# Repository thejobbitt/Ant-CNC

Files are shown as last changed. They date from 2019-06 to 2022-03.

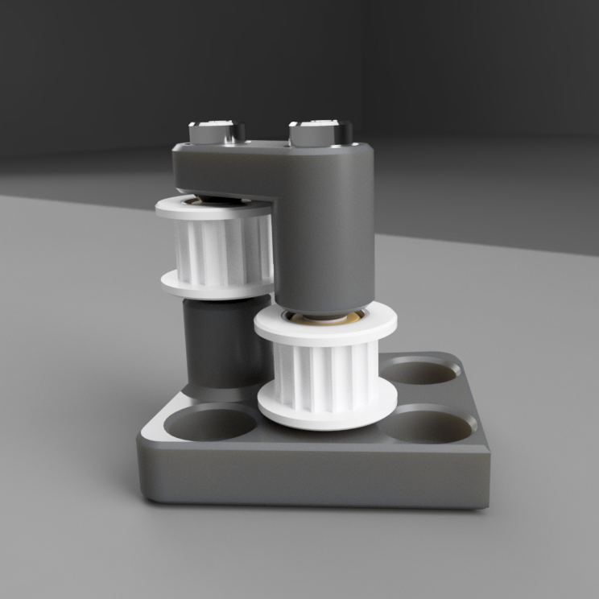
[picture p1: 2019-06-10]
images/wiki/GT2 Pulley Support Assembly v5.png

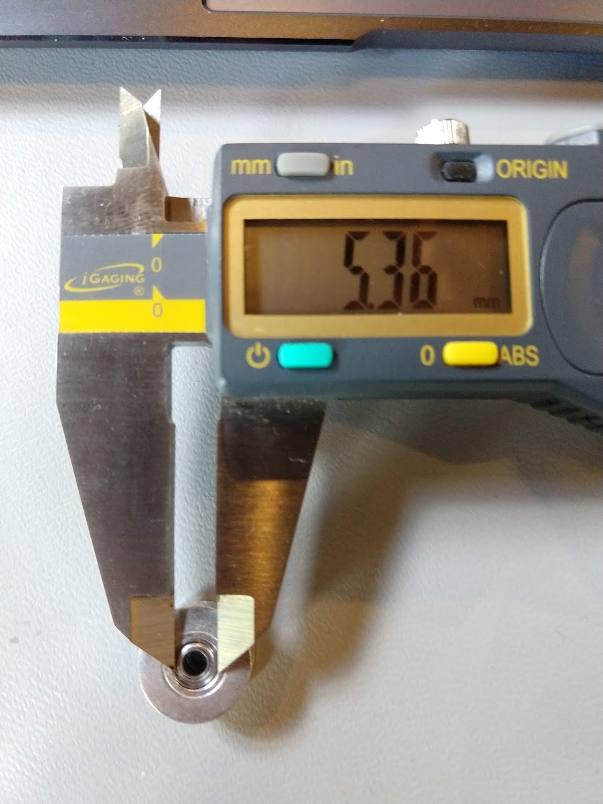
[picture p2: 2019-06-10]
images/wiki/outer_race_GT2_16T.jpg

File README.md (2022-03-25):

# Ant-CNC
Unofficial Ant CNC

This is a place to store the information I gather while building the Ant CNC. None of the upgrades are tested. Use at your own risk.

Any updates I make will be released with Fusion 360 files. If you wish to add to this repository send me a message.

Official github      -> https://github.com/TheAntTeam  
Official release     -> https://bitbucket.org/compactpcbmaker/cpcbm/src/master/  
Official youtube     -> https://www.youtube.com/channel/UCX44z-SSL7LzcB4xxgUdHHA/videos  
Official reddit      -> https://www.reddit.com/r/TheANT/  
Official facebook    -> https://www.facebook.com/groups/2238987226122714/  
Thingiverse Upgrades -> https://www.thingiverse.com/search?q=ant+pcb  

NOTE: All the files and informations in the mechanics folder of this repository are licensed under CC-BY-NC-SA license.

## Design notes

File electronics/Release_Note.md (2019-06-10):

14-04-2019 Modified Connection Scheme presentation.
Added also the link to the electronics assembly video as a reference, and added some more specific comments about:

-Nucleo F401RE board cap removal

-X and Y limit switches connections and checks.

-Spindle spinning direction.

12-02-2019 Added Connection Scheme presentation first draft.

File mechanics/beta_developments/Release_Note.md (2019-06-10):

# 23-04-2019
This is the Beta Developments folder where we share parts not yet released and under test.

Added head_4p2, an head modified to work with the Mistery D2632 blue and red version and brushless with up to 28 mm diameter.

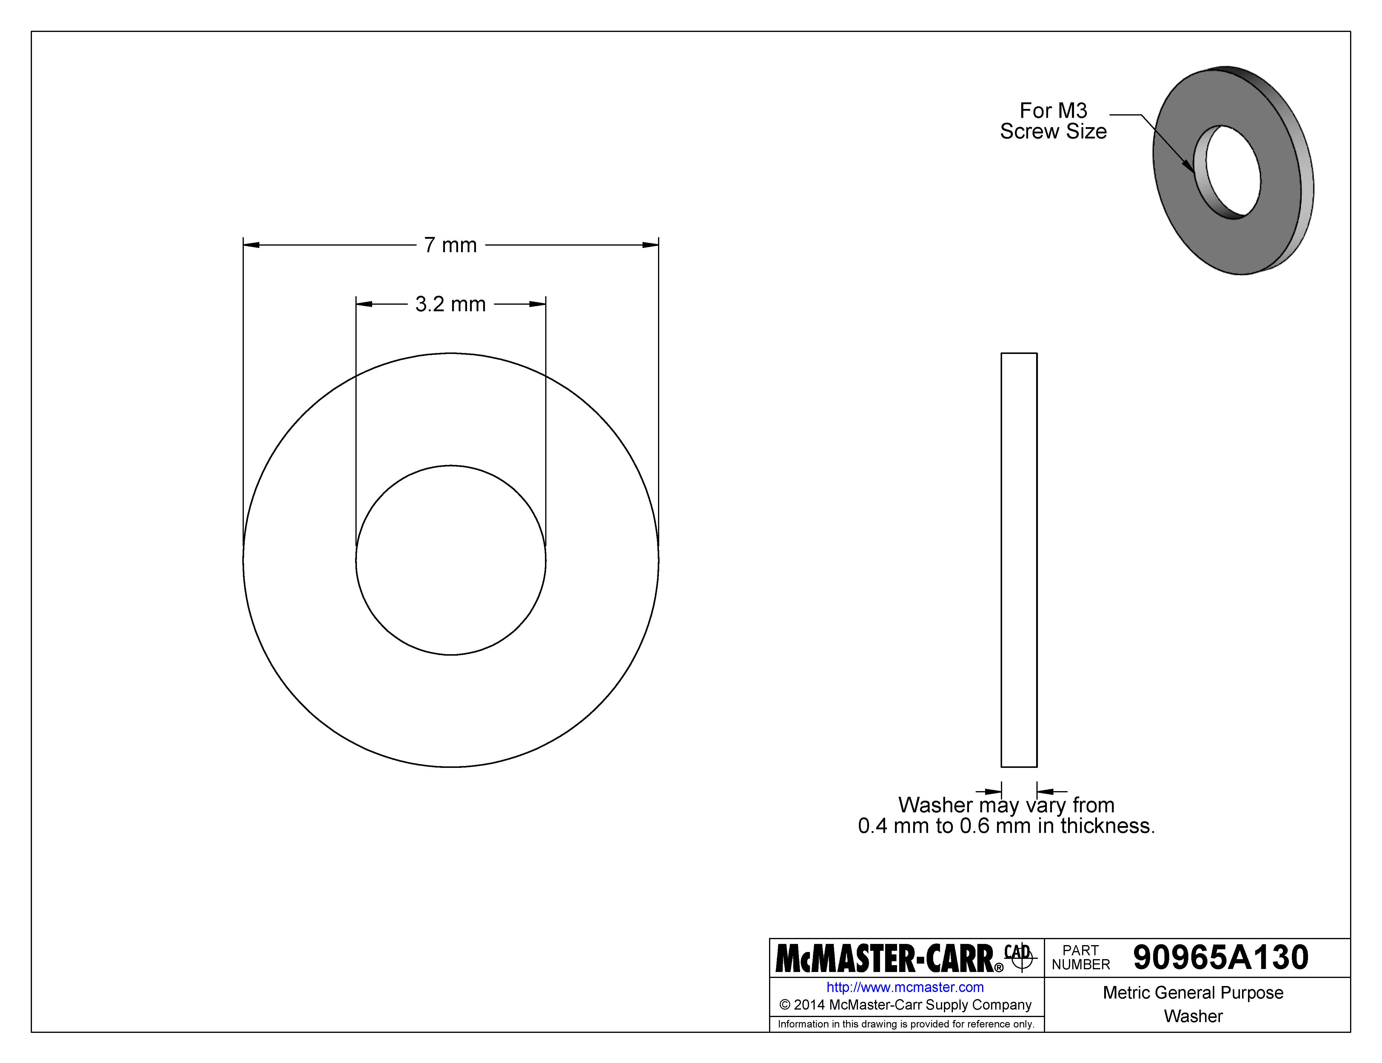
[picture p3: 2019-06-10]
images/wiki/3mm_flat_washer.jpg

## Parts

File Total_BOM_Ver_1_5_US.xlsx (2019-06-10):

Item | 1 | 2 | 3 | 4 | 5 | 6 | Qty | Brand | Ordered From | Part # | Cost | Qty if Pack | Unit Cost | Build Cost | Notes
Frame
10 x 10 x 200mm Aluminum Profile (black) | 8 |  |  |  |  |  | 8 | Makerbeam (kit) | Amazon | 100012 | $112.50 | 1 | 112.5 | $112.50
10 x 10 x 60mm Aluminum Profile (black) | 4 |  |  |  |  |  | 4 |  | ^
10 x 10mm Stainless Right Angle Bracket | 8 |  |  |  |  |  | 8 |  | ^
M3 x 0.5 x 6mm Square Headed Bolt | 47 |  |  |  |  |  | 47 |  | ^
Makerbeam T-slot nut | 24 |  |  |  |  |  | 24 | Makerbeam | Amazon | 101619 | $17.00 | 25 | 0.68 | $16.32
Hardware
M3 x 0.5 mm Lock Nut | 46 | 9 |  | 2 |  |  | 57 |  | McMaster | 90576A102 | $3.45 | 100 | 0.0345 | $1.97
M3 x 0.5mm Hex Nut | 4 |  |  |  |  | 8 | 12 |  | McMaster | 90591A250 | $2.21 | 100 | 0.0221 | $0.27
M5 x 0.8mm Hex Nut |  |  |  | 1 |  | 2 | 3 |  | McMaster | 90591A260 | $2.80 | 100 | 0.028 | $0.08
M2 x 0.4 x 8mm Socket Cap Bolt |  |  |  |  | 2 |  | 2 |  | McMaster | 91292A832 | $6.00 | 100 | 0.06 | $0.12
M2.5 x 0.45 x 8mm Socket Cap Bolt |  |  |  | 8 |  |  | 8 |  | McMaster | 91292A012 | $5.15 | 100 | 0.0515 | $0.41
M4 x 0.5 x 4mm Button Head Bolts (ISO 7380) | 8 |  |  |  | 4 |  | 12 |  | McMaster | 91239A109 | $8.50 | 25 | 0.34 | $4.08
M3 x 0.5 x 6mm Socket Cap Bolt | 12 | 9 |  | 2 | 3 |  | 26 |  | McMaster | 91292A111 | $9.18 | 100 | 0.0918 | $2.39
M3 x 0.5 x 8mm Socket Cap Bolt |  |  |  |  | 4 |  | 4 |  | McMaster | 91292A112 | $4.29 | 100 | 0.0429 | $0.17
M3 x 0.5 x 10mm Socket Cap Bolt |  | 4 |  |  |  | 8 | 12 |  | McMaster | 91292A113 | $4.72 | 100 | 0.0472 | $0.57
M3 x 0.5 x 16mm Socket Cap Bolt | 2 |  |  |  | 4 |  | 6 |  | McMaster | 91292A115 | $5.58 | 100 | 0.0558 | $0.33
M3 x 0.5 x 20mm Socket Cap Bolt | 8 |  |  | 1 |  |  | 9 |  | McMaster | 91292A123 | $6.44 | 100 | 0.0644 | $0.58
M3 x 0.5 x 25mm Socket Cap Bolt |  |  |  | 2 |  |  | 2 |  | McMaster | 91292A020 | $6.87 | 100 | 0.0687 | $0.14
M3 x 0.5 x 30mm Socket Cap Bolt | 4 |  |  |  |  |  | 4 |  | McMaster | 91292A022 | $4.08 | 50 | 0.0816 | $0.33
M3 x 0.5 x 50mm Socket Cap Bolt |  | 2 |  |  | 4 |  | 6 |  | McMaster | 91292A026 | $3.76 | 25 | 0.1504 | $0.90
M5 x 0.8 x 16mm Hex Head Bolt |  |  |  |  |  | 2 | 2 |  | McMaster | 91287A124 | $6.73 | 50 | 0.1346 | $0.27
M3 Lock Washer (ID 3mm, OD 5.5mm) | 8 | 14 |  |  |  |  | 22 |  | McMaster | 93925A220 | $3.45 | 100 | 0.0345 | $0.76
M3 Washer (ID 3mm, OD 7.5mm) | 16 | 10 |  |  |  |  | 26 |  | McMaster | 91166A210 | $1.69 | 100 | 0.0169 | $0.44
M3 x 0.5 x 100mm Threaded Rod |  | 3 |  |  |  |  | 3 | EasyScope | AliExpress |  | $2.89 | 5 | 0.578 | $1.73
3 x 16mm (#4 - 5/8") Flat Wood Screw |  |  |  |  |  | 6 | 6 | Midwest Fastner | Menards | 2524 | $2.13 | 100 | 0.0213 | $0.13 | Local
Bearings and Rails
GT2 Pulley 16T, 3mm Bore, 6mm Belt (w/ Bearings) | 4 | 2 |  |  |  |  | 6 | Powge | AliExpress |  | $12.60 | 7 | 1.8 | $10.80
GT2 Pulley, No Teeth, ID 3mm, 6mm Belt (w/ Bearings) |  | 2 |  |  |  |  | 2 | Powge | AliExpress |  | $5.40 | 3 | 1.8 | $3.60
GT2 Pulley 16T, ID 5mm, 6mm Belt, Set Screw (w/ Bearings) |  |  |  | 2 |  |  | 2 | Powge | AliExpress |  | $4.99 | 5 | 0.998 | $2.00
GT2 Timing Belt, 6mm Width, 1 Meter Length |  |  |  | 2 |  |  | 2 | Powge | AliExpress |  | $1.99 | 1 | 1.99 | $3.98
GT2 Timing Belt Locking Torsion Spring | 2 |  |  |  |  |  | 2 | Ali Life Store | AliExpress | SKU135539-3 FFIO PCK | $1.65 | 20 | 0.0825 | $0.16 | Check type
MGN9H Linear Rail 9mm x 200 mm | 2 |  |  |  |  |  | 2 | CNA Mecchanical Parts | AliExpress |  | $10.80 | 1 | 10.8 | $21.60
LM6UU Bearing |  | 8 |  |  |  |  | 8 | uxcell | Amazon | 709874355093 | $12.01 | 10 | 1.201 | $9.61
706C Bearing |  | 2 |  |  |  |  | 2 | Mochu | AliExpress |  | $5.00 | 1 | 5 | $10.00
6 x 180mm Chrome Plated Rod (200mm is Okay) |  | 2 |  |  |  |  | 2 | CNC Factory | AliExpress |  | $3.66 | 2 | 1.83 | $3.66
6 x 100mm Chrome Plated Rod |  | 2 |  |  |  |  | 2 | CNC Factory | AliExpress |  | $2.61 | 2 | 1.305 | $2.61
Spindle
ER8M C6 60L Extension Rod Chuck (w/ 1/8" Spring Collet) |  |  |  | 1 |  |  | 1 | HOZLY | AliExpress |  | $12.59 | 1 | 12.59 | $12.59
Lock Collar (Ring) w/ Set Screw, ID 6 mm, OD 12mm, 8mm Width |  |  |  | 1 |  |  | 1 | Victory 3D | AliExpress |  | $0.39 | 1 | 0.39 | $0.39
O-Ring ID 17mm, 2mm Thick |  |  |  |  |  | 2 | 2 | Hands Online | AliExpress |  | $0.36 | 10 | 0.036 | $0.07
Motors
NEMA - 11 - JK28HS51-674 |  |  | 2 |  |  |  | 2 | StepperOnline | Amazon | 11HS18-0674S | $18.90 | 1 | 18.9 | $37.80
Z Axis Stepper Linear Actuator - LC1574W-04-025 |  |  |  | 1 |  |  | 1 | Haydon | eBay | LC1574W-04-025 | $14.50 | 1 | 14.5 | $14.50
M12 Nut w/ Step 1.75mm, 5mm Thick (Included with Actuator) |  |  |  | 1 |  |  | 1 |  | ^
1000KV 2632 Brushless Outrunner Motor |  |  | 1 |  |  |  | 1 | Mistery | AliExpress | 2632-1000 | $25.39 | 1 | 25.39 | $25.39
Electronics
ESC 20A (for Brushless) |  |  | 1 |  |  |  | 1 | Gallop RC | AliExpress |  | $9.12 | 1 | 9.12 | $9.12
Nucleo F401RE |  |  |  |  | 1 |  | 1 | ST | Digikey |  | $13.83 | 1 | 13.83 | $13.83
CNC Arduino Shield V3 |  |  |  |  | 1 |  | 1 | Witbot (kit) | Amazon |  | $11.99 | 1 | 11.99 | $11.99
Stepstick Stepper Driver (A4988) |  |  |  |  | 3 |  | 3 |  | ^
2.54mm Jumper |  |  |  |  | 10 |  | 10 |  | ^
Mechanical Limit Switch Module Vertical |  | 2 |  |  |  |  | 2 | H X Y | AliExpress |  | $1.58 | 1 | 1.58 | $3.16
Mechanical Endstop Micro Switch w/ Dupont Terminal |  |  | 1 |  |  |  | 1 | AirMail | AliExpress |  | $1.51 | 1 | 1.51 | $1.51
Round Rocker Switch, SPST, 12v, 14mm panel hole |  |  |  |  | 1 |  | 1 | USMEI | Amazon |  | $6.49 | 2 | 3.245 | $3.25
12V brushless 40x40x10mm fan |  |  |  |  | 1 |  | 1 | Noctua | Amazon | NF-A4x10 | $13.95 | 1 | 13.95 | $13.95
12V 10A Power Supply, 5.5mm x 2.5mm DC Plug |  |  |  |  |  | 1 | 1 | COOLM | Amazon | HJDZ-1210 | $21.99 | 1 | 21.99 | $21.99
Wire and Connectors
3.5mm Bullet Connector Male |  |  | 3 |  |  |  | 3 | Apex RC | Amazon | 1102 | $7.99 | 10 | 0.799 | $2.40
3.5mm Bullet Connectors Female |  |  | 2 |  |  |  | 2 | Apex RC | ^
JST 1x04 Connector Male |  |  | 1 |  |  |  | 1 | Hilitch | Amazon |  | $10.69 | 200 | 0.05345 | $0.05
Dupont 1x04 Connector Female Housing |  |  | 2 |  |  |  | 2 | FUNMANY (kit) | Amazon |  | $13.99 | 200 | 0.06995 | $0.14
Dupont 1x03 Connector Female Housing |  |  | 2 |  |  |  | 2 |  | ^
Dupont Female Pin |  |  | 14 |  |  |  | 14 |  | ^
Alligator Clip w/ Cover |  |  | 2 |  |  |  | 2 |  | McMaster | 7236K55 | $0.94 | 1 | 0.94 | $1.88
Extension Servo Lead Wire Male to Female 10 cm cable |  |  | 1 |  |  |  | 1
Cable 26 AWG about 40 cm |  |  | 4 |  |  |  | 4
Cable 16 AWG about 40 cm |  |  | 2 |  |  |  | 2
Cable 16 AWG about 20 cm |  |  |  |  | 2 |  | 2
Dupont cable Female to Female 20 cm |  |  |  |  | 2 |  | 2
5.5mm x 2.1mm DC Power Jack, Barrel, Panel Mount |  |  |  |  | 1 |  | 1 | Switchcraft | Digikey | SC3508-ND | $3.99 | 1 | 3.99 | $3.99
3.5mm Stereo earphone with jack 3.5mm |  |  | 1 |  |  |  | 1 | CUI Inc | Digikey | MP3-3501 | $1.04 | 1 | 1.04 | $1.04
3.5mm Stereo Headphone Jack, Panel Mount |  |  |  |  | 1 |  | 1 | Nine to Nine | Amazon |  | $6.99 | 10 | 0.699 | $0.70
Other
Heat Shrink Tube (Various sizes) |  |  |  |  |  |  | 1 | Gardner Bender | Ace Hardware | 3429057 | $13.99 | 1 | 13.99 | $13.99 | Local
5" Black Cable Ties 100 Pack |  |  |  | 4 |  |  | 4 | Store House | Harbor Freight | 60254 | $1.99 | 100 | 0.0199 | $0.08 | Local
Sheath Spiral Tube, ID 6mm, OD 8mm, 1m Long |  |  |  |  | 1 |  | 1 | Uxcell | Amazon |  | $8.01 | 8 | 1.00125 | $1.00
MDF Board 240Lx150Wx10mmH (9-1/2"L x 5-7/8"W x 1/2"H) |  |  |  | 1 |  |  | 1 |  | Menards | 1272032 | $8.27 | 1 | 8.27 | $8.27 | Local
Roll of PETG Filament |  |  |  |  |  |  | 1 | 3D Solutech (https://www.amazon.com/gp/product/B01A6ORBGA/ref=ppx_yo_dt_b_asin_title_o04_s00?ie=UTF8&psc=1) | Amazon |  | $20.99 | 1 | 20.99 | $20.99
 |  |  |  |  |  |  |  |  |  |  | $531.60 |  |  | $436.57

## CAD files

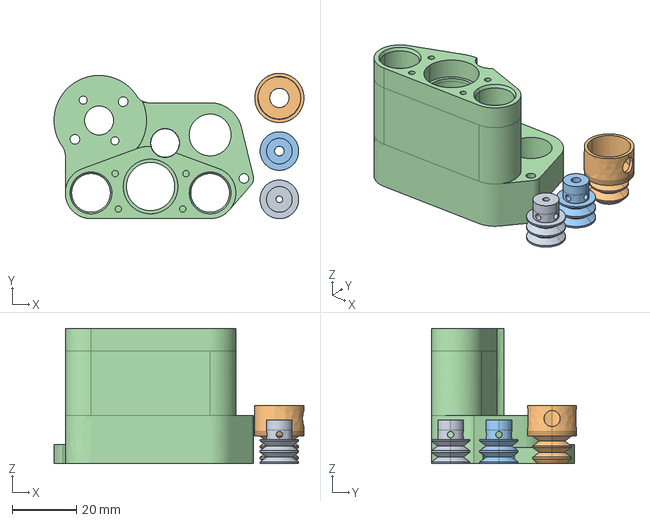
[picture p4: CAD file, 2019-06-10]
mechanics/beta_developments/head_4p2_beta.stp
77.6 x 45.1 x 42.0 mm

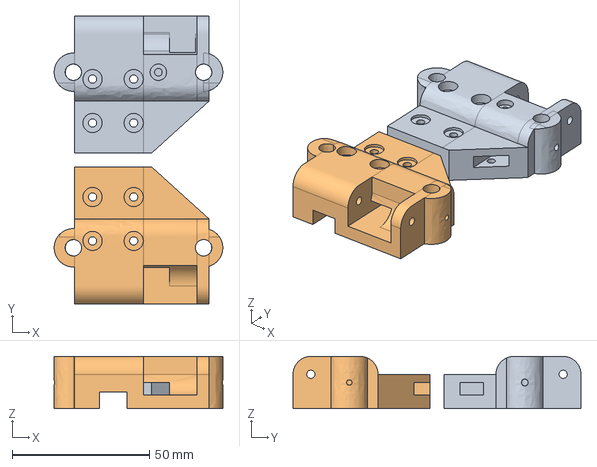
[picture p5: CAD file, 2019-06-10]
mechanics/bridge/bridge_right_and_left_1p2.stp
61.5 x 105.0 x 19.0 mm

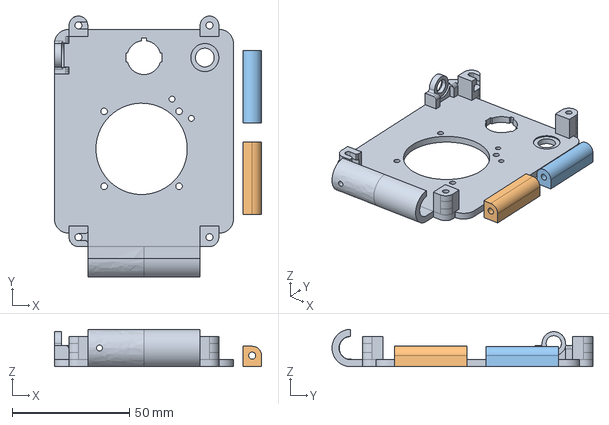
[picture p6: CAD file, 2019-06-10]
mechanics/electronics_and_accessories/nucleo_cover_1p4.stp
88.5 x 111.5 x 16.0 mm

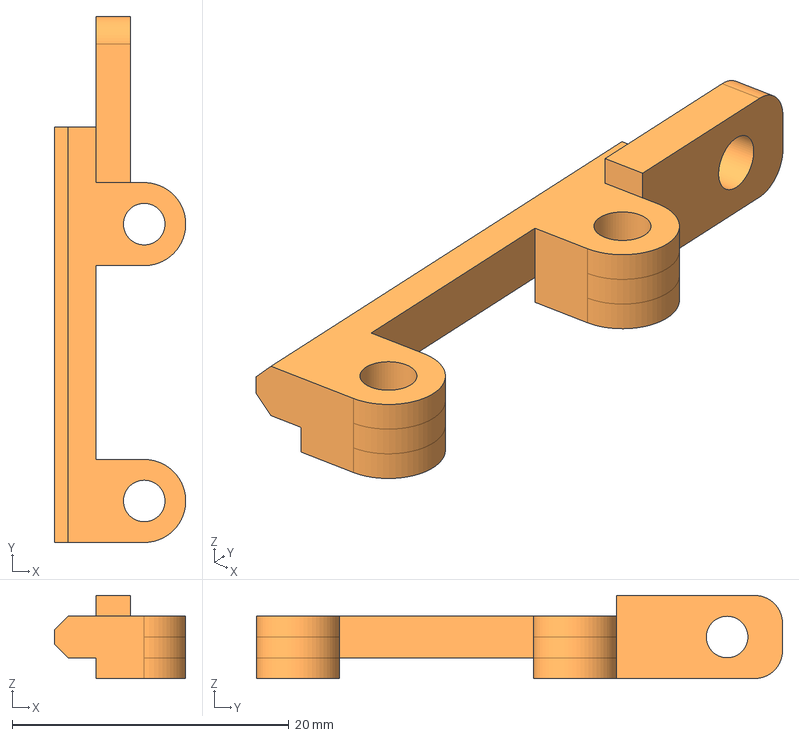
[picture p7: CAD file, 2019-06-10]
mechanics/frame/limit_y_support_1p0.stp
9.50 x 38.0 x 6.00 mm

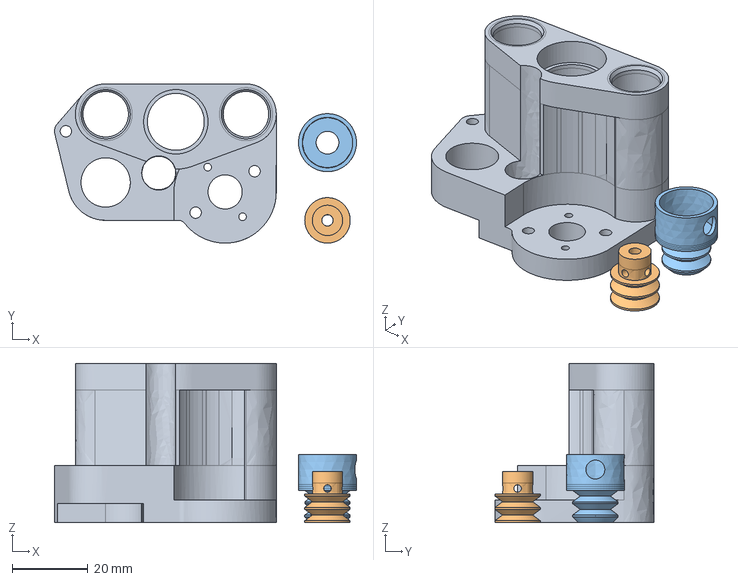
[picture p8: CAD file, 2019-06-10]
mechanics/head/head_4p1.stp
79.6 x 42.0 x 42.0 mm

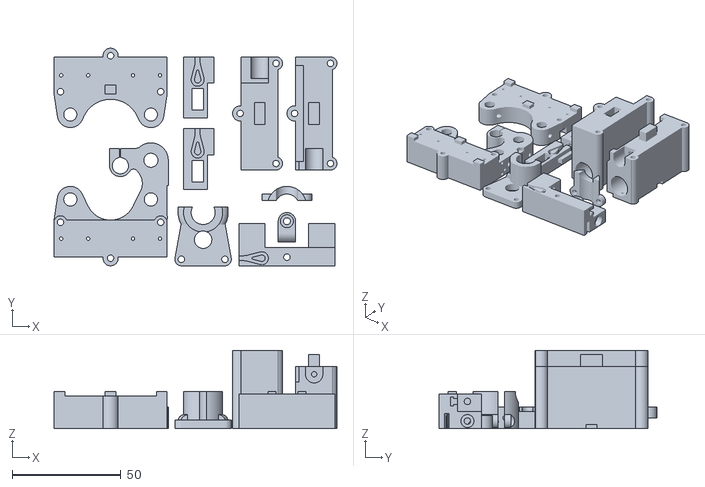
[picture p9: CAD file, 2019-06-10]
mechanics/bridge/bridge_2p2.stl
130.0 x 100.0 x 36.0

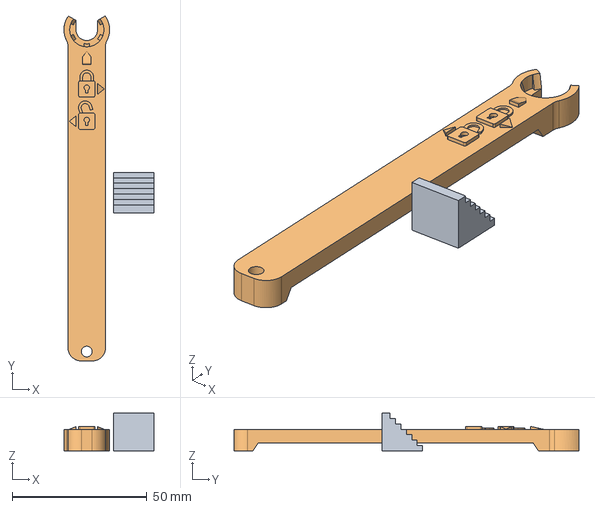
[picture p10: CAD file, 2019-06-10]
mechanics/electronics_and_accessories/change_tools_1p0.stp
33.5 x 128.1 x 14.0 mm

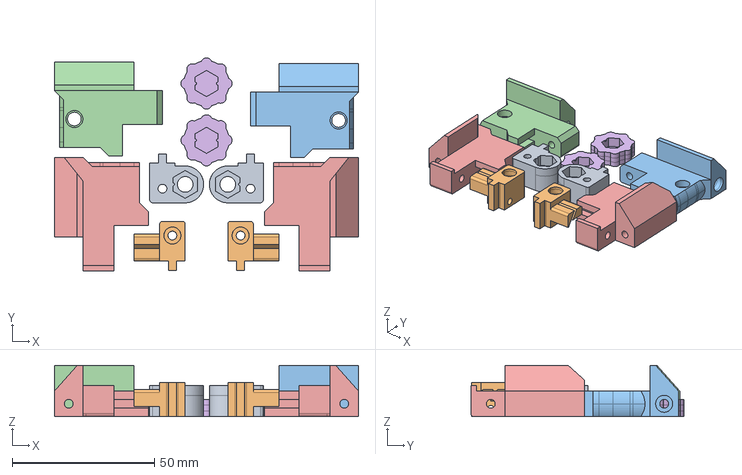
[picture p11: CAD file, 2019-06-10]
mechanics/frame/bed_holder_1p3.stp
107.0 x 75.0 x 18.0 mm

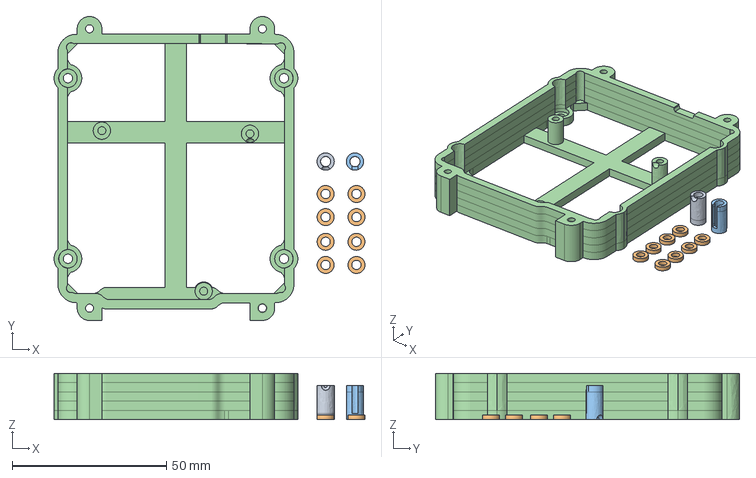
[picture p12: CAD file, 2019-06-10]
mechanics/electronics_and_accessories/nucleo_back_1p4.stp
100.8 x 98.5 x 15.0 mm

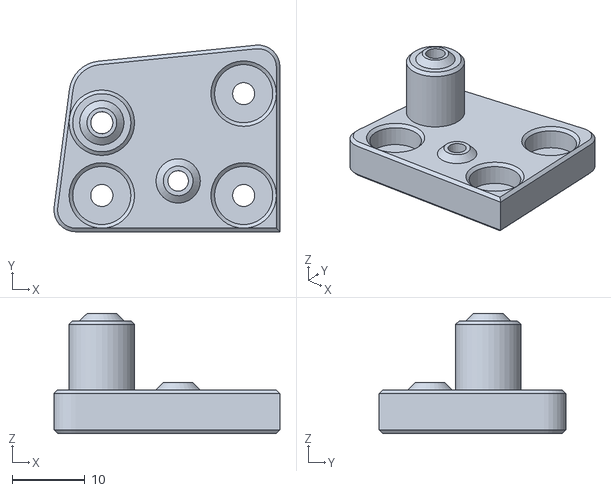
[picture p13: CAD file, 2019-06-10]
mechanics/frame/GT2_pulley_support_right_i2.stl
31.1 x 25.7 x 16.5

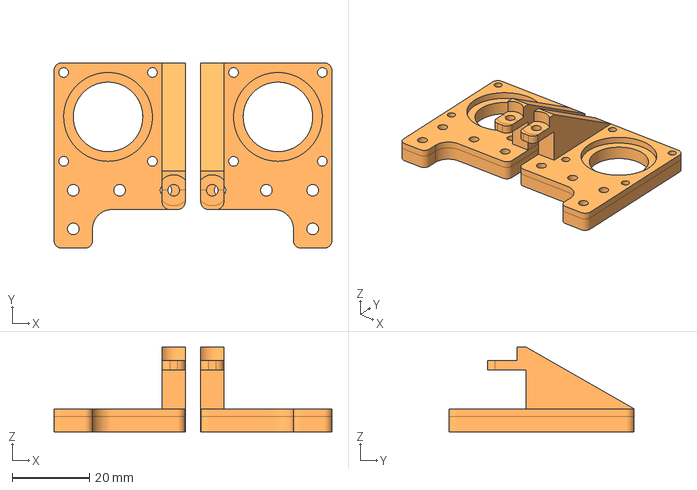
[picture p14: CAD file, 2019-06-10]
mechanics/frame/motor_holder_1p0.stp
72.0 x 48.0 x 22.0 mm

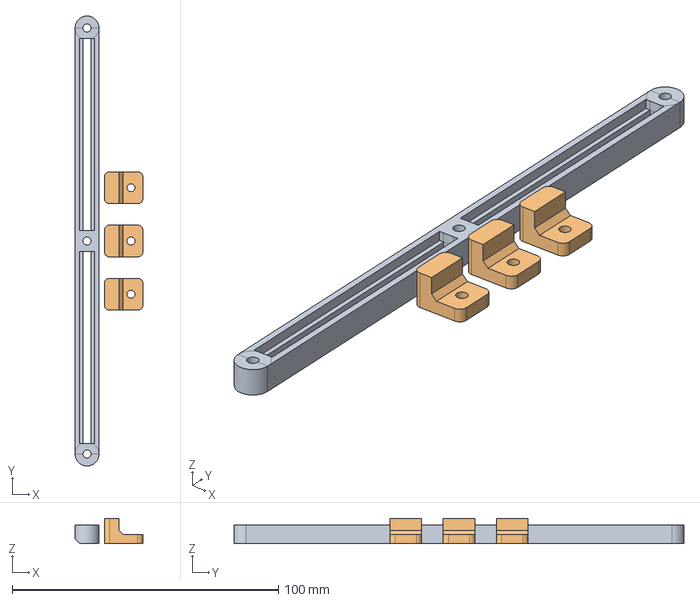
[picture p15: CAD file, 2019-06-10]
mechanics/frame/pcb_lock_1p0.stp
25.5 x 169.0 x 9.50 mm

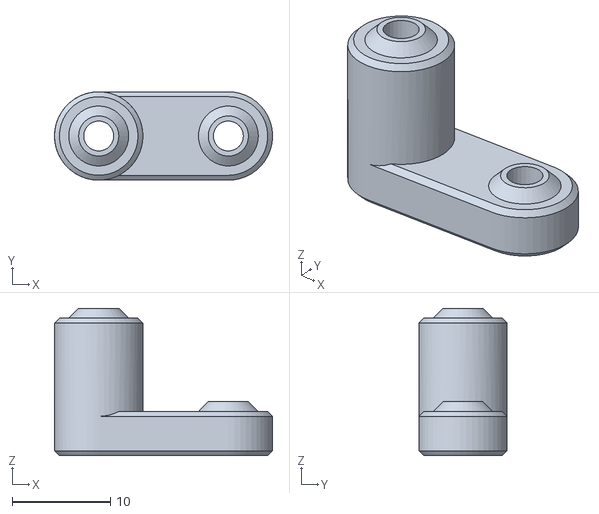
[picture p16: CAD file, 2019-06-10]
mechanics/frame/GT2_pulley_upper_support_i2.stl
22.2 x 9.00 x 15.0

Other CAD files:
mechanics/frame/GT2_pulley_support_left_i2.stl
mechanics/beta_developments/head_4p2_beta.stl
mechanics/bridge/bridge_right_and_left_1p2.stl
mechanics/electronics_and_accessories/change_tools_1p0.stl
mechanics/electronics_and_accessories/nucleo_back_1p4.stl
mechanics/electronics_and_accessories/nucleo_cover_1p4.stl
mechanics/frame/GT2_pulley_support_left_i2 v5.f3d
mechanics/frame/GT2_pulley_support_right_i2 v12.f3d
mechanics/frame/GT2_pulley_upper_support_i2 v3.f3d
mechanics/frame/limit_y_support_1p0.stl
mechanics/frame/motor_holder_1p0.stl
mechanics/frame/pcb_lock_1p0.stl
mechanics/head/head_4p1.stl

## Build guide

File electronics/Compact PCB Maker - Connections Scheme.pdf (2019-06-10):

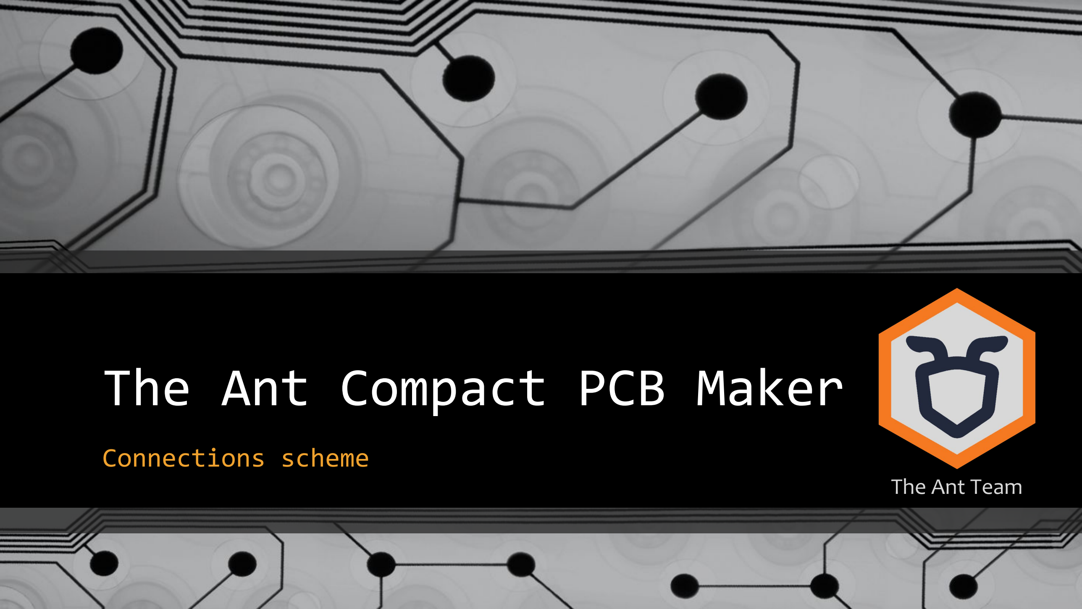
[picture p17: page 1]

# The Ant Compact PCB Maker

### Connections scheme

The Ant Team

# Introduction

## This document shows how to connect the different electronics parts of The Ant Machine. We strongly suggests you to watch these videos:

## https://youtu.be/eRefCvD_KVs

as a preparation for this stage of machine construction,

## https://youtu.be/ptuefynbbEo

as connection instructions.

# Electronics central unit parts

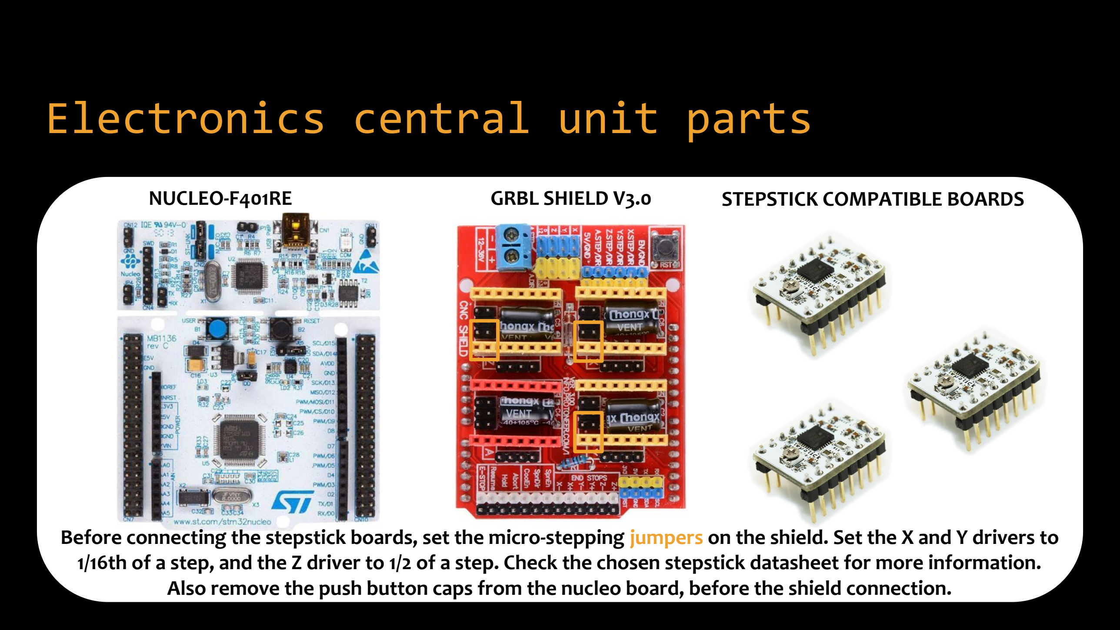
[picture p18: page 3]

Before connecting the stepstick boards, set the micro-stepping jumpers on the shield. Set the X and Y drivers to 1/16th of a step, and the Z driver to 1/2 of a step. Check the chosen stepstick datasheet for more information. Also remove the push button caps from the nucleo board, before the shield connection.

NUCLEO-F401RE | GRBL SHIELD V3.0 | STEPSTICK COMPATIBLE BOARDS

# Power Supply

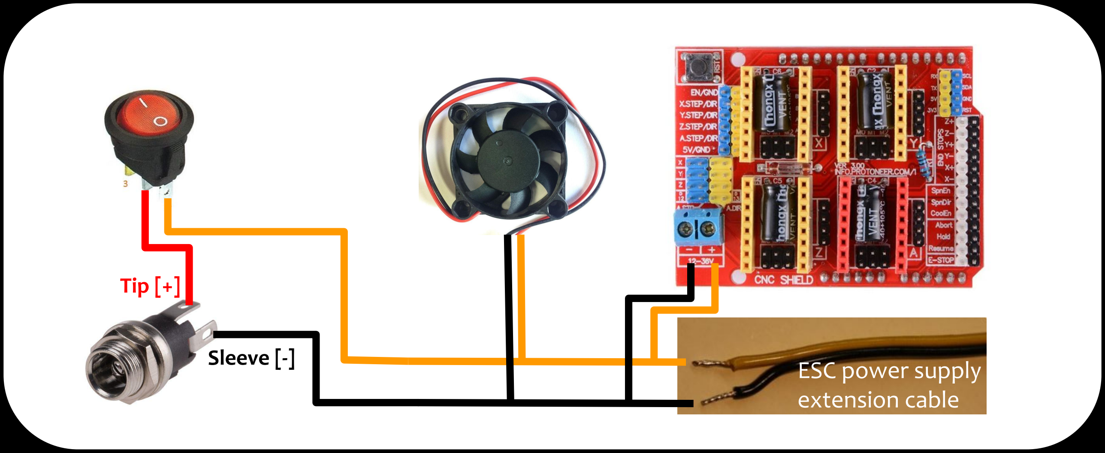
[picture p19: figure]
ESC power supply extension cable; Sleeve [-]; Tip [+]

# ESC Power Supply

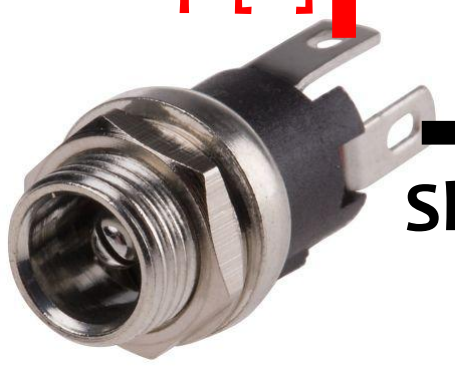
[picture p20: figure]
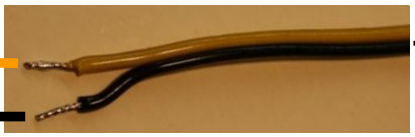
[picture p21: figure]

Sleeve [-]

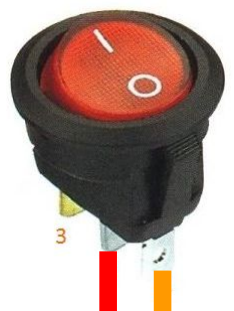
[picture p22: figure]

Tip [+]

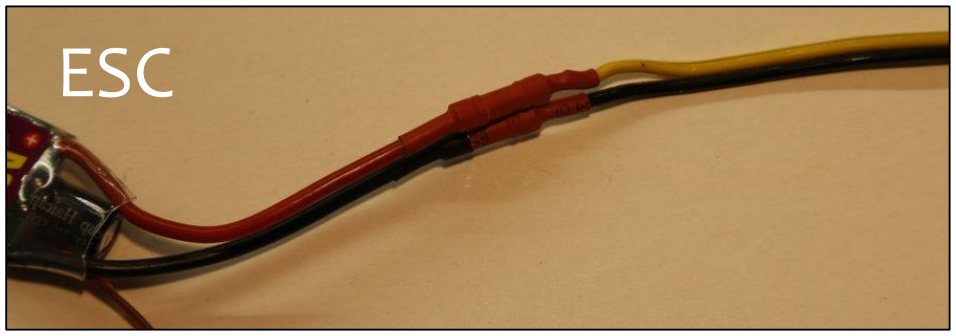
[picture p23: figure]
ESC

# CoreXY Stepper Motors

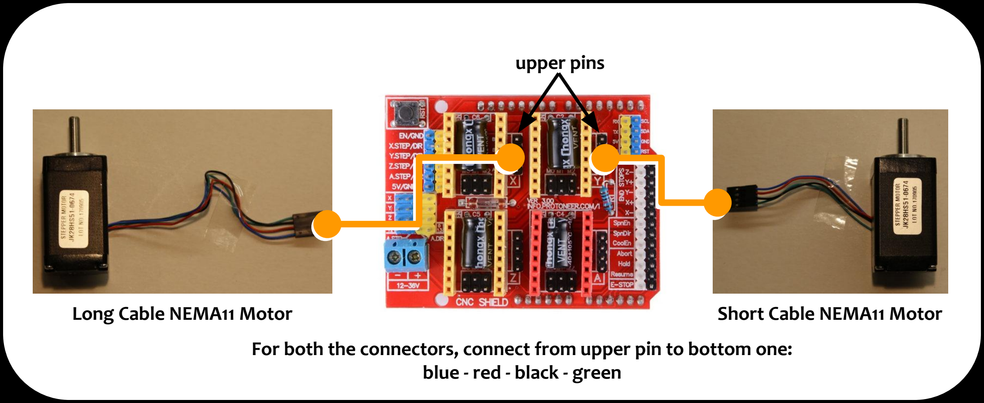
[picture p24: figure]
blue - red - black - green; upper pins; Long Cable NEMA11 Motor; Short Cable NEMA11 Motor

For both the connectors, connect from upper pin to bottom one:

# Z axis Stepper Motor

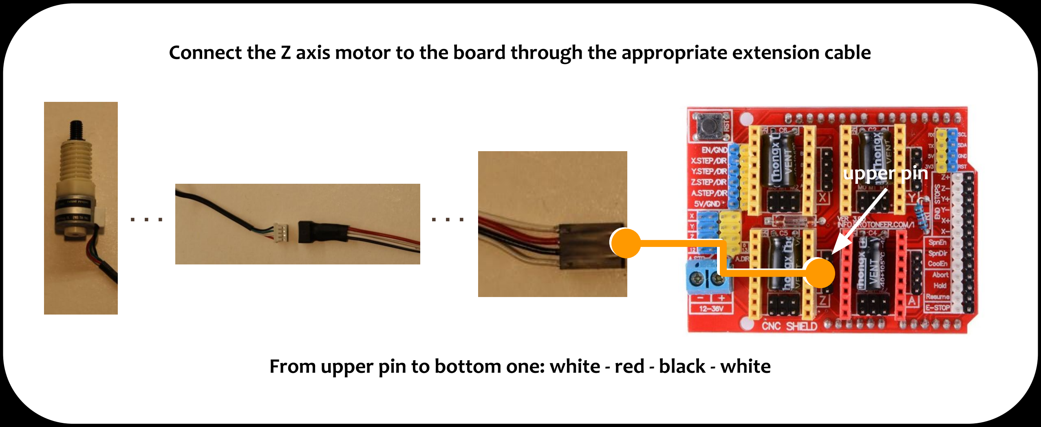
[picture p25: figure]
upper pin

From upper pin to bottom one: white - red - black - white

Connect the Z axis motor to the board through the appropriate extension cable

# Z axis Limit Switch

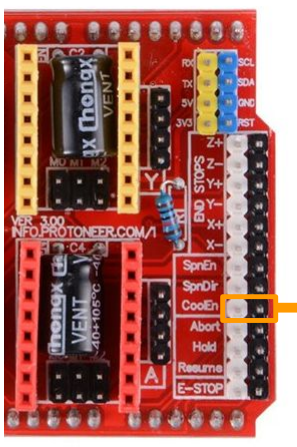
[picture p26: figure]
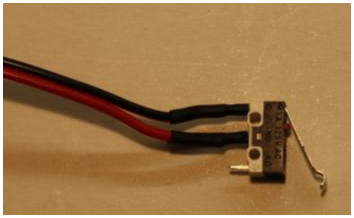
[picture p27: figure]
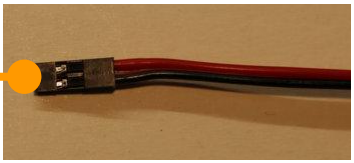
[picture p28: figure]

Black ground wire connected to the right pin, signal red wire connected to the left pin

# Y axis Limit Switch

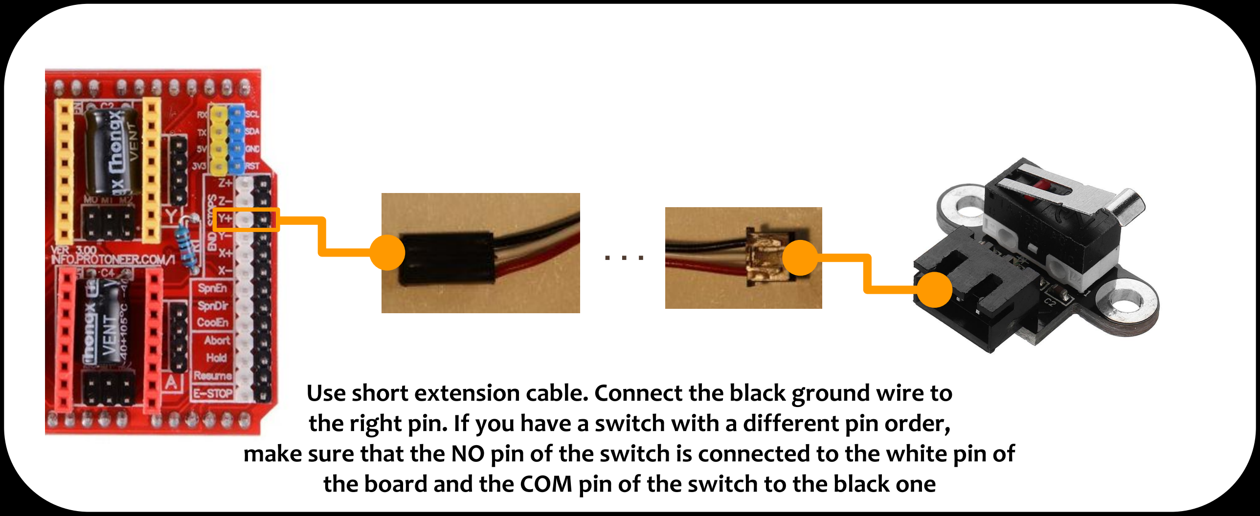
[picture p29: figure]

Use short extension cable. Connect the black ground wire to the right pin. If you have a switch with a different pin order, make sure that the NO pin of the switch is connected to the white pin of the board and the COM pin of the switch to the black one

# X axis Limit Switch

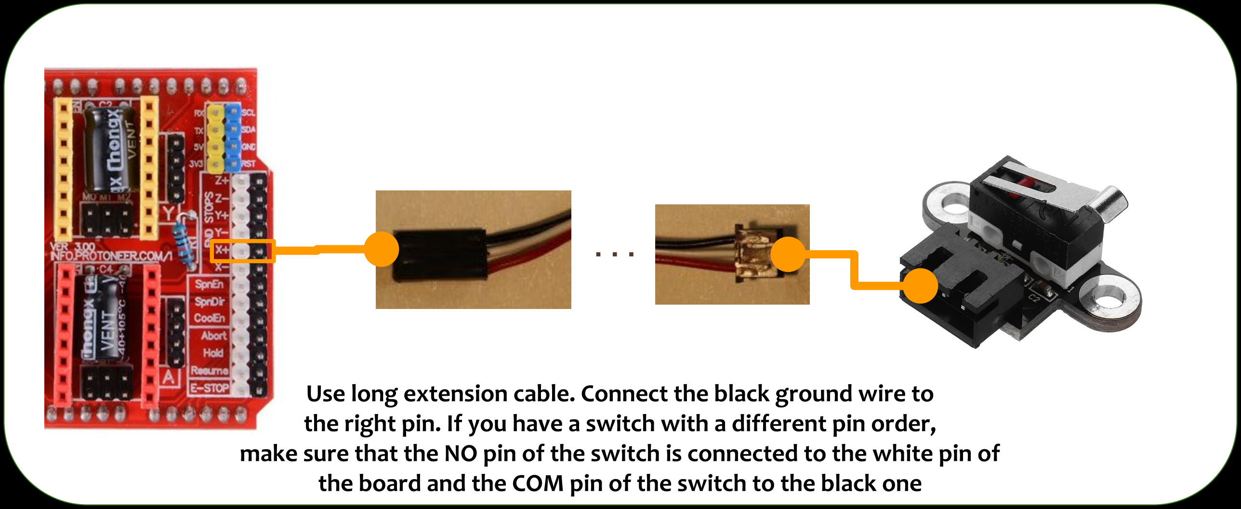
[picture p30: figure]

Use long extension cable. Connect the black ground wire to the right pin. If you have a switch with a different pin order, make sure that the NO pin of the switch is connected to the white pin of the board and the COM pin of the switch to the black one

# Spindle PWM control

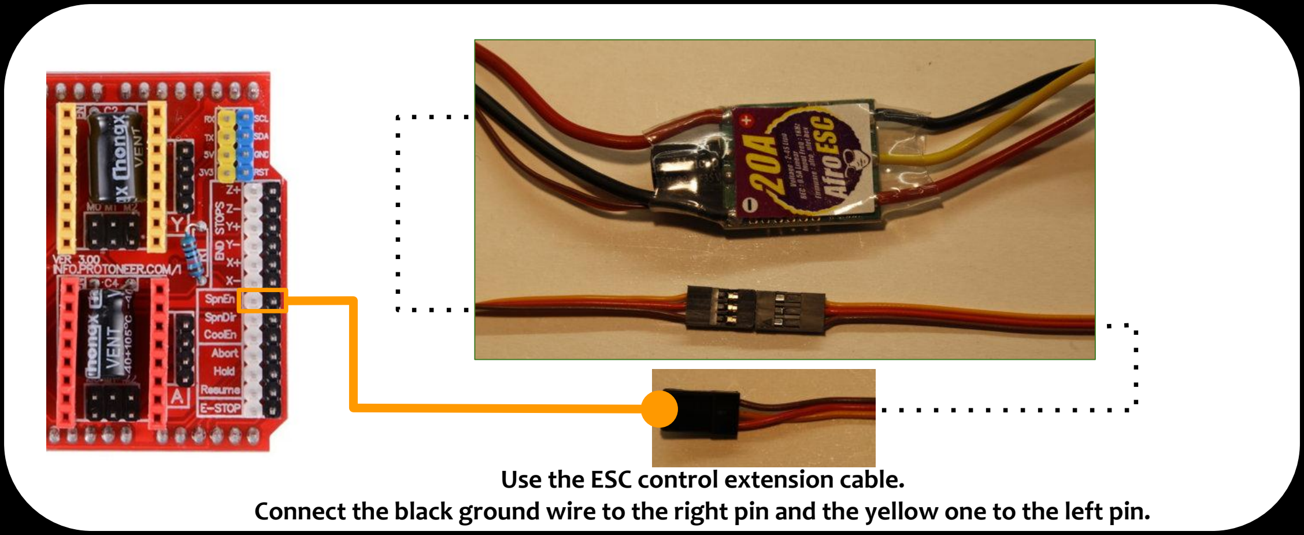
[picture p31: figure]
Use the ESC control extension cable.

Connect the black ground wire to the right pin and the yellow one to the left pin.

# Spindle ESC to brushless

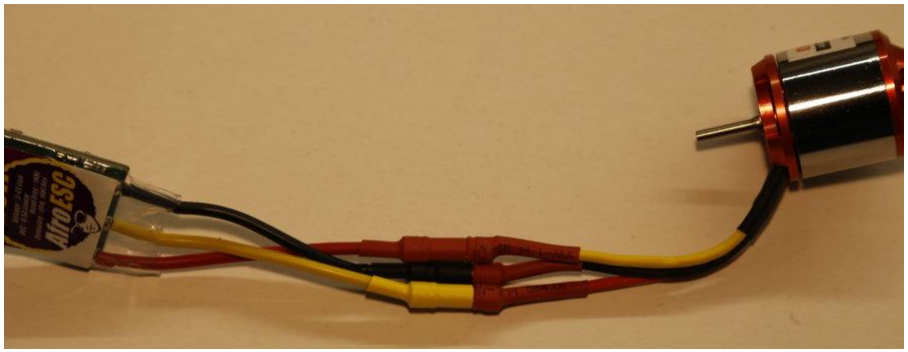
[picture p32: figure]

Check the connections. For our configuration Red and Yellow wire must be inverted. The machining bit has to spin clockwise looking at it from the top of the machine.

# Probe jack connector

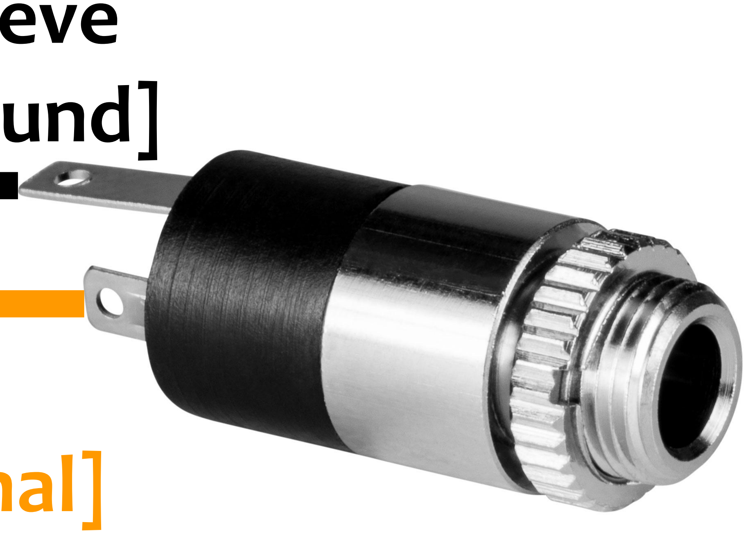
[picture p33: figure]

Sleeve
[ground]

Tip
[probe signal]

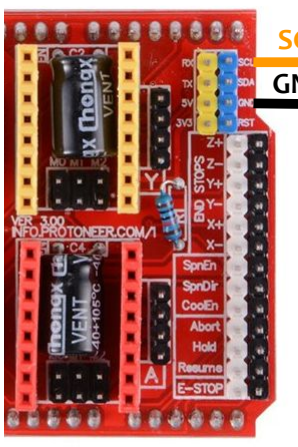
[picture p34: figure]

SCL
GND

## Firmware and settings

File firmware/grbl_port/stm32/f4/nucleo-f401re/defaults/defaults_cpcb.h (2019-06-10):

/*
  defaults_cpcb.h - defaults settings configuration file for Compact PCB Maker machine.
  Part of grbl_port_opencm3 project.

  Copyright (c) 2017 Angelo Di Chello

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
  You should have received a copy of the GNU General Public License
  along with Grbl_port_opencm3.  If not, see <http://www.gnu.org/licenses/>.
*/

/* The defaults.h file serves as a central default settings file for different machine
   types, from DIY CNC mills to CNC conversions of off-the-shelf machines. The settings
   here are supplied by users, so your results may vary. However, this should give you
   a good starting point as you get to know your machine and tweak the settings for your
   nefarious needs. */


//#ifndef GRBL_PORT_STM32_F4_NUCLEO_F401RE_GRBL_DEFAULTS_DEFAULTS_CPCB_H_
//#define GRBL_PORT_STM32_F4_NUCLEO_F401RE_GRBL_DEFAULTS_DEFAULTS_CPCB_H

#ifndef defaults_h
#define defaults_h

  // Grbl generic default settings. Should work across different machines.
  #define DEFAULT_X_STEPS_PER_MM 100.0
  #define DEFAULT_Y_STEPS_PER_MM 100.0
  #define DEFAULT_Z_STEPS_PER_MM 100.0
  #define DEFAULT_X_MAX_RATE 1000.0 // mm/min
  #define DEFAULT_Y_MAX_RATE 1000.0 // mm/min
  #define DEFAULT_Z_MAX_RATE 500.0 // mm/min
  #define DEFAULT_X_ACCELERATION (10.0*60*60) // 10*60*60 mm/min^2 = 10 mm/sec^2
  #define DEFAULT_Y_ACCELERATION (10.0*60*60) // 10*60*60 mm/min^2 = 10 mm/sec^2
  #define DEFAULT_Z_ACCELERATION (10.0*60*60) // 10*60*60 mm/min^2 = 10 mm/sec^2
  #define DEFAULT_X_MAX_TRAVEL 200.0 // mm
  #define DEFAULT_Y_MAX_TRAVEL 200.0 // mm
  #define DEFAULT_Z_MAX_TRAVEL 200.0 // mm
  #define DEFAULT_STEP_PULSE_MICROSECONDS 10
  #define DEFAULT_STEPPING_INVERT_MASK 0
  #define DEFAULT_DIRECTION_INVERT_MASK 0
  #define DEFAULT_STEPPER_IDLE_LOCK_TIME 255 // msec (0-254, 255 keeps steppers enabled)
  #define DEFAULT_STATUS_REPORT_MASK ((BITFLAG_RT_STATUS_MACHINE_POSITION)|(BITFLAG_RT_STATUS_WORK_POSITION))
  #define DEFAULT_JUNCTION_DEVIATION 0.01 // mm
  #define DEFAULT_ARC_TOLERANCE 0.002 // mm
  #define DEFAULT_REPORT_INCHES 0 // false
  #define DEFAULT_INVERT_ST_ENABLE 0 // false
  #define DEFAULT_INVERT_LIMIT_PINS 0 // false
  #define DEFAULT_SOFT_LIMIT_ENABLE 0 // false
  #define DEFAULT_HARD_LIMIT_ENABLE 1  // false
  #define DEFAULT_HOMING_ENABLE 1  // true
  #define DEFAULT_HOMING_DIR_MASK 0 // move positive dir
  #define DEFAULT_HOMING_FEED_RATE 25.0 // mm/min
  #define DEFAULT_HOMING_SEEK_RATE 500.0 // mm/min
  #define DEFAULT_HOMING_DEBOUNCE_DELAY 250 // msec (0-65k)
  #define DEFAULT_HOMING_PULLOFF 1.0 // mm

#endif /* GRBL_PORT_STM32_F4_NUCLEO_F401RE_GRBL_DEFAULTS_DEFAULTS_CPCB_H */

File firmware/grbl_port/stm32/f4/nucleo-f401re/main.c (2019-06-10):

/*
  main.c - An embedded CNC Controller with rs274/ngc (g-code) support
  Part of grbl_port_opencm3 project, derived from the Grbl work.

  Copyright (c) 2017 Angelo Di Chello
  Copyright (c) 2011-2015 Sungeun K. Jeon
  Copyright (c) 2009-2011 Simen Svale Skogsrud
  
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
  You should have received a copy of the GNU General Public License
  along with Grbl_port_opencm3.  If not, see <http://www.gnu.org/licenses/>.
*/

#include "grbl.h"


// Declare system global variable structure
system_t sys; 


int main(void)
{
#ifdef NUCLEO_F401
#ifndef BASIC_CPU_SPEED
	const struct rcc_clock_scale rcc_hse_8mhz_3v3_no_prescalers =
	{ /* 48MHz */
		.pllm = 8,
		.plln = 96,
		.pllp = 2,
		.pllq = 2,
		.hpre = RCC_CFGR_HPRE_DIV_NONE,
		.ppre1 = RCC_CFGR_PPRE_DIV_NONE,
		.ppre2 = RCC_CFGR_PPRE_DIV_NONE,
		.voltage_scale = PWR_SCALE1,
		.flash_config = FLASH_ACR_ICEN | FLASH_ACR_DCEN |
				FLASH_ACR_LATENCY_3WS,
		.ahb_frequency  = 48000000,
		.apb1_frequency = 48000000,
		.apb2_frequency = 48000000
	};
//  rcc_clock_setup_hse_3v3(&rcc_hse_8mhz_3v3[RCC_CLOCK_3V3_84MHZ]);
	rcc_clock_setup_hse_3v3(&rcc_hse_8mhz_3v3_no_prescalers);
#endif
#endif
  // Initialize system upon power-up.
  serial_init();   // Setup serial baud rate and interrupts
  settings_init(); // Load Grbl settings from EEPROM
  stepper_init();  // Configure stepper pins and interrupt timers
  system_init();   // Configure pinout pins and pin-change interrupt

  memset(&sys, 0, sizeof(system_t));  // Clear all system variables
  sys.abort = true;   // Set abort to complete initialization
#ifdef NUCLEO_F401
  __enable_irq(); // Global enable interrupts
#else
  sei(); // Enable interrupts
#endif

  // Check for power-up and set system alarm if homing is enabled to force homing cycle
  // by setting Grbl's alarm state. Alarm locks out all g-code commands, including the
  // startup scripts, but allows access to settings and internal commands. Only a homing
  // cycle '$H' or kill alarm locks '$X' will disable the alarm.
  // NOTE: The startup script will run after successful completion of the homing cycle, but
  // not after disabling the alarm locks. Prevents motion startup blocks from crashing into
  // things uncontrollably. Very bad.
  #ifdef HOMING_INIT_LOCK
    if (bit_istrue(settings.flags,BITFLAG_HOMING_ENABLE)) { sys.state = STATE_ALARM; }
  #endif
  
  // Force Grbl into an ALARM state upon a power-cycle or hard reset.
  #ifdef FORCE_INITIALIZATION_ALARM
    sys.state = STATE_ALARM;
  #endif
  
  // Grbl initialization loop upon power-up or a system abort. For the latter, all processes
  // will return to this loop to be cleanly re-initialized.
  for(;;) {

    // TODO: Separate configure task that require interrupts to be disabled, especially upon
    // a system abort and ensuring any active interrupts are cleanly reset.
  
    // Reset Grbl primary systems.
    serial_reset_read_buffer(); // Clear serial read buffer
    gc_init(); // Set g-code parser to default state
    spindle_init();
    coolant_init();
    limits_init(); 
    probe_init();
    plan_reset(); // Clear block buffer and planner variables
    st_reset(); // Clear stepper subsystem variables.

#ifdef VARIABLE_SPINDLE
    /* Check if a minimal pwm needs to be given to the spindle at startup
       As an example, this is useful when using something like an ESC to
       control the spindle motor and the ESC needs a small input PWM to be
       activated. */
    if(settings.spindle_pwm_enable_at_start)
    {
    	// Enable Clockwise spindle with minimal pwm
    	gc_state.modal.spindle = SPINDLE_ENABLE_CW;
    	spindle_set_state(SPINDLE_ENABLE_CW, 0);
    }
#endif

    // Sync cleared gcode and planner positions to current system position.
    plan_sync_position();
    gc_sync_position();

    // Reset system variables.
    sys.abort = false;
    sys_rt_exec_state = 0;
    sys_rt_exec_alarm = 0;
    sys.suspend = false;
    sys.soft_limit = false;
              
    // Start Grbl main loop. Processes program inputs and executes them.
    protocol_main_loop();
    
  }
  return 0;   /* Never reached */
}

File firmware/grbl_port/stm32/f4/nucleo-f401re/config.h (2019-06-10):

/*
  config.h - compile time configuration
  Part of grbl_port_opencm3 project, derived from the Grbl work.

  Copyright (c) 2017 Angelo Di Chello
  Copyright (c) 2012-2015 Sungeun K. Jeon
  Copyright (c) 2009-2011 Simen Svale Skogsrud

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
  You should have received a copy of the GNU General Public License
  along with Grbl_port_opencm3.  If not, see <http://www.gnu.org/licenses/>.
*/
  
// This file contains compile-time configurations for Grbl's internal system. For the most part,
// users will not need to directly modify these, but they are here for specific needs, i.e.
// performance tuning or adjusting to non-typical machines.

// IMPORTANT: Any changes here requires a full re-compiling of the source code to propagate them.

#ifndef CONFIG_H
#define CONFIG_H
//#include "grbl.h" // For Arduino IDE compatibility.


// Default settings. Used when resetting EEPROM. Change to desired name in defaults.h
#define DEFAULTS_CPCB

// Default pwm spindle parameters. Used when resetting EEPROM. Change to desired name in pwm_spindle_params.h
#define PWM_SPINDLE_PARAMS_AFRO20

// Serial baud rate
#define BAUD_RATE 115200

// Default cpu mappings. Grbl officially supports the Arduino Uno only. Other processor types
// may exist from user-supplied templates or directly user-defined in cpu_map.h
//#define CPU_MAP_ATMEGA328P // Arduino Uno CPU
#define NUCLEO_F401 // Nucleo F401 board

// Define realtime command special characters. These characters are 'picked-off' directly from the
// serial read data stream and are not passed to the grbl line execution parser. Select characters
// that do not and must not exist in the streamed g-code program. ASCII control characters may be 
// used, if they are available per user setup. Also, extended ASCII codes (>127), which are never in 
// g-code programs, maybe selected for interface programs.
// NOTE: If changed, manually update help message in report.c.
#define CMD_STATUS_REPORT '?'
#define CMD_FEED_HOLD '!'
#define CMD_CYCLE_START '~'
#define CMD_RESET 0x18 // ctrl-x.
#define CMD_SAFETY_DOOR '@'

// If homing is enabled, homing init lock sets Grbl into an alarm state upon power up. This forces
// the user to perform the homing cycle (or override the locks) before doing anything else. This is
// mainly a safety feature to remind the user to home, since position is unknown to Grbl.
#define HOMING_INIT_LOCK // Comment to disable

// Define the homing cycle patterns with bitmasks. The homing cycle first performs a search mode
// to quickly engage the limit switches, followed by a slower locate mode, and finished by a short
// pull-off motion to disengage the limit switches. The following HOMING_CYCLE_x defines are executed 
// in order starting with suffix 0 and completes the homing routine for the specified-axes only. If
// an axis is omitted from the defines, it will not home, nor will the system update its position.
// Meaning that this allows for users with non-standard cartesian machines, such as a lathe (x then z,
// with no y), to configure the homing cycle behavior to their needs. 
// NOTE: The homing cycle is designed to allow sharing of limit pins, if the axes are not in the same
// cycle, but this requires some pin settings changes in cpu_map.h file. For example, the default homing
// cycle can share the Z limit pin with either X or Y limit pins, since they are on different cycles.
// By sharing a pin, this frees up a precious IO pin for other purposes. In theory, all axes limit pins
// may be reduced to one pin, if all axes are homed with seperate cycles, or vice versa, all three axes
// on separate pin, but homed in one cycle. Also, it should be noted that the function of hard limits 
// will not be affected by pin sharing.
// NOTE: Defaults are set for a traditional 3-axis CNC machine. Z-axis first to clear, followed by X & Y.
//#define HOMING_CYCLE_0 (1<<Z_AXIS)                // REQUIRED: First move Z to clear workspace.
//#define HOMING_CYCLE_1 ((1<<X_AXIS)|(1<<Y_AXIS))  // OPTIONAL: Then move X,Y at the same time.

#define HOMING_CYCLE_0 (1<<Z_AXIS)
#define HOMING_CYCLE_1 (1<<Y_AXIS)                // COREXY REQUIRED: First move Y.
#define HOMING_CYCLE_2 (1<<X_AXIS)                // COREXY REQUIRED: Then move X.

//#define HOMING_CYCLE_0 (1<<X_AXIS)                // COREXY REQUIRED: First move x.
//#define HOMING_CYCLE_1 (1<<Y_AXIS)                // COREXY REQUIRED: Then move Y.

// #define HOMING_CYCLE_2                         // OPTIONAL: Uncomment and add axes mask to enable

// Number of homing cycles performed after when the machine initially jogs to limit switches.
// This help in preventing overshoot and should improve repeatability. This value should be one or 
// greater.
#define N_HOMING_LOCATE_CYCLE 1 // Integer (1-128)
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

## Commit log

2019-06-10 Initial Push
    Includes GT2 Pulley Support Update
    [GT2_pulley_support_1p0.stl, GT2_pulley_support_1p0.stp, GT2_pulley_support_left_i2 v5.f3d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]
2019-06-10 Readme update.
    [GT2_pulley_support_1p0.stl, GT2_pulley_support_1p0.stp]

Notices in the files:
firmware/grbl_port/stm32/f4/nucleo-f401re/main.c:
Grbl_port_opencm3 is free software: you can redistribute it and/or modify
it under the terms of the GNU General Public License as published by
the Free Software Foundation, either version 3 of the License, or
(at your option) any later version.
